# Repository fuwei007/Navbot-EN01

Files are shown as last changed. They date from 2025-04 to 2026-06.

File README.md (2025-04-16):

# NavBot-EN01 Wheeled_leg-Robot
> **The tabletop the tabletop robot**
>
> Vedio:[....](......)

| Real Robot | 3D Design |
| --- | --- |
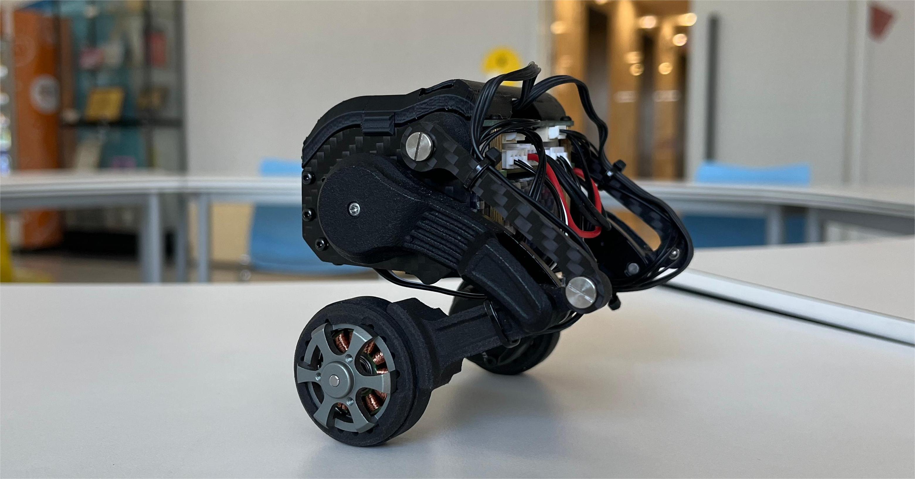
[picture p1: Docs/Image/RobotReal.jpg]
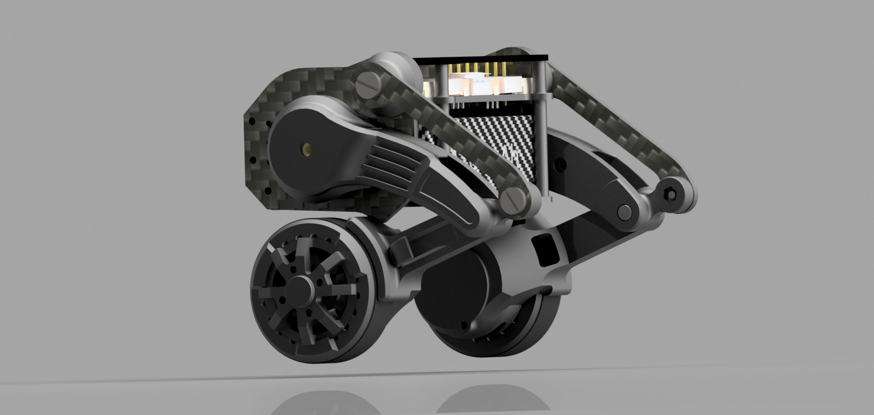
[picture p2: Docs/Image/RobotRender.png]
|  |  |

### Mechanical Structure Documentation

* The file "OriginalRobotModel.stp" is the robot model file.
* The "Parts-Manufactured" folder contains parts that need to be processed and produced by yourself, including 3D printing, CNC, and panel cutting.
* The "Parts-Purchased" folder contains parts that need to be purchased.

### PCB Documentation

* There are four PCBs that need to be fabricated; the circuit boards provide both the schematic and PCB source files, and the IDE used is [LCEDA](https://lceda.cn/).
* The main control board is based on the ESP32, with the brushless motor driver chip being the L6234PD013TR. 
* The encoder chip used is the AS5600, communicating with the main control board via the I2C interface.
* The IMU used is the MPU6050 module, which shares the same I2C interface with the right-side encoder.
* The servo debugging board unifies the two serial lines into one signal line, completing the task through time-division multiplexing to send and receive data.
* In addition, you will need three GH1.25 4PIN double-ended cables, with a recommended length of 15cm. These need to be purchased separately.

| Wire Connection | 
| ------------ |
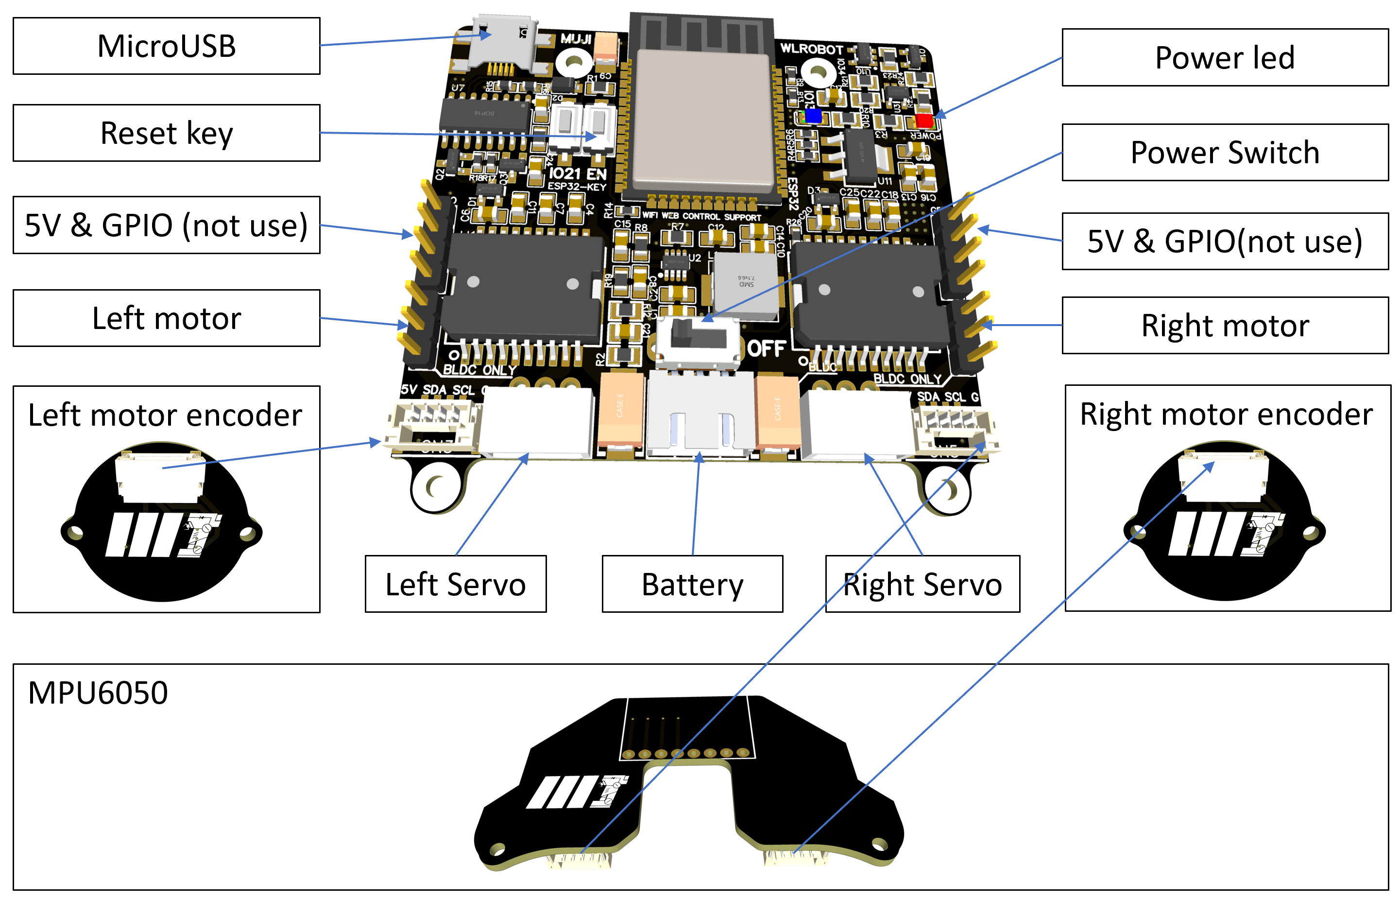
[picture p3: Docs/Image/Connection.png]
|  |

### Source Code Usage

* Based on [Arduino IDE](https://www.arduino.cc/), it is very easy to learn and use.
* The brushless motor drive for the wheels is based on [simpleFOC](https://www.simplefoc.com/#simplefoc_library).
* The left bus servo ID is 1, and the right is 2; the calibration for the legs to fully squat to the mechanical limit position is 2048; configuration is done using [FEETECH Debug Software](https://gitee.com/ftservo/fddebug).
* The [ESP32](https://www.espressif.com/sites/default/files/documentation/esp32_datasheet_en.pdf) itself has WiFi capabilities, with the webpage code stored in flash, transmitting JSON data via the WebSocket communication protocol.
* Please use the WebSocket library located in [3.Software/libraries](3.Software/libraries). The recommended esp32 version is 2.0.3.
* There are two WiFi models, AP mode and STA mode. AP mode uses the device as a wireless hotspot, and STA mode uses the device as a client to connect to an existing wireless network.

### Usage Instructions

* 1. Connect the battery's XH2.54 plug to the rear interface of the main control board and turn on the switch to power the robot.
* 2. After turning on the switch, a red light on the main board will indicate that the power is on.
* 3. Next, the wheels will start FOC motor initialization, with the wheels moving slightly and the legs starting to move.
* 4. If the battery is sufficient, the blue LED on the main control board will light up. If it does not light up, charging is needed.
* 5. After this process is complete, press the EN button on the main control board to restart, and you can then connect to the robot's WiFi network starting with WL. The password is the lowercase WiFi name.
* 6. Open a browser and go to the URL 192.168.1.11. The remote control interface is compatible with Android, iOS, Windows, Linux, macOS, etc., and it is recommended to use Chrome or Firefox.
* 7. Manually stabilize the robot, with the wheels slightly touching the ground. Click the "Robot go!" button on the web page, and the robot will stand up. You can then control the robot's movement using the joystick.

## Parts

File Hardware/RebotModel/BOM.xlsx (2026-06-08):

Part Name | Recommended Purchase Link | Specifications | Quantity | Price($)
Servo | https://www.amazon.com/magnetic-rotating-minibus-steering-black/dp/B0BP645PF9 | 1pcs ST3032 all metal hollow cup 360 degree magnetic coding rotating TTL signal level minibus steering gear (black) | 2 | 110
Motor | https://www.amazon.com/Fityle-Gimbal-Brushless-100-200g-Quadcopter/dp/B07JLSL8ZV | Fityle 2208 90KV 3mm Shaft Gimbal Brushless Motor for 100-200g Gopro3 RC Quadcopter | 2 | 16.31
Neodymium Magnet | https://www.amazon.com/TRYMAG-Magnets-Neodymium-Whiteboard-Billboard/dp/B09SL2K4BP | TRYMAG 340Pcs Small 4x1mm Mini Neodymium Magnets | 2 | 8.99
Battery | https://www.amazon.com/MakerHawk-Rechargeable-Protection-Connector-Electronic/dp/B0D9K7HQHT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 | MakerHawk 4 Pack 3.7V 1000mAh LiPo Battery Rechargeable | 1 | 18.99
Screw M2*4 | https://www.amazon.com/iexcell-Thread-Socket-Screws-Finish/dp/B0D4JM92FW | iexcell 100 Pcs M2 x 4mm | 20 | 7.86
Screw M2*6 | https://www.amazon.com/iexcell-Thread-Socket-Screws-Finish/dp/B0D4JMMJ9M | iexcell 100 Pcs M2 x 6mm | 10 | 7.86
Screw M2.5*5 | https://www.amazon.com/iexcell-Thread-Socket-Screws-Finish/dp/B0DDXRMGCW | iexcell 100 Pcs M2.5 x 5mm | 10 | 7.86
Screw M3*6 | https://www.amazon.com/iexcell-Thread-Socket-Screws-Finish/dp/B07GGXKW1Y | iexcell 250 Pcs M3 x 6 | 4 | 9.86
BigHead Screw M2*6 | https://www.amazon.com/iexcell-Thread-Socket-Screws-Finish/dp/B0D4JMMJ9M | iexcell 100 Pcs M2 x 6mm | 4 | 7.86
Nut M2 | https://www.amazon.com/pouilzx-Carbon-Steel-Hexagon-200pcs/dp/B0CMG7Q27P | M2 Carbon Steel Grade 8 Hexagon Hex Nut Black Carbon Steel | 10 | 5.99
Screw M2.3*15 | https://www.amazon.com/uxcell-Stainless-Phillips-Tapping-Screws/dp/B01M0DCMHQ | uxcell 100 Pcs M2.5 x 15mm Stainless Steel Phillips Round Head Self Tapping Screws Bolts | 2 | 9.29
Earings 3-6-2 | https://www.amazon.com/Hobbypark-Bearings-Shielded-Quadcopter-Helicopter/dp/B019F2ZH92 | 10pcs Hobbypark Micro Ball Bearings 3x6x2mm | 4 | 8.97
Earings 4-7-2.5 | https://www.amazon.com/4x7x2-5-Shielded-Precision-Miniature-Bearings/dp/B085RD75QY | 10 Pack 4x7x2.5 Metal Shielded ABEC-5 High Precision Miniature Ball Bearings L-740ZZ (MR74ZZ) | 4 | 9.49
Cylindrical Pin 4x12 | https://www.amazon.com/uxcell-Stainless-Cylindrical-Support-Elements/dp/B07YKYJZ63 | uxcell 4 x 12mm(Approx 5/32") Dowel Pin 304 Stainless Steel Wood Bunk Bed Dowel Pins Shelf Pegs Support Shelves 25Pcs | 2 | 7.69
Brass Standoff M2*8+3 | https://www.amazon.com/MECCANIXITY-Standoffs-Assortment-Raspberry-Motherboard/dp/B0FH1FTF5J | MECCANIXITY M2 Male Brass Hex Spacer Standoffs Screws Nuts, 20 Set Hex Column Screw Nut Assortment Kit M2*8+3 Threaded Standoff | 2 | 7.69
Brass Standoff M2*25+4 | https://www.amazon.com/PATIKIL-Standoff-Quadcopter-Motherboard-Computer/dp/B0DWF384DG | PATIKIL M2 x 20+3 mm Male Female Brass Hex Spacer Standoff | 2 | 5.09
Brass Standoff M2*8 | https://www.amazon.com/uxcell-Straight-Pillar-Standoff-M2x3x8mm/dp/B07H3SR8XX | uxcell 50pcs Brass Round Straight PCB Pillar Female Thread Standoff Spacer M2x3x8mm | 2 | 7.59
Brass Standoff M2*3*3 | https://www.amazon.com/uxcell-116pcs-Straight-Standoff-M2x3x3mm/dp/B07H3XJ7BB?sp_csd=d2lkZ2V0TmFtZT1zcF9hdGY | uxcell 116pcs Brass Round Straight PCB Pillar Female Thread Standoff Spacer M2x3x3mm | 4 | 8.59
Tire（Round Silicone Ring） | https://www.amazon.com/Rubber-Assorted-Camping-Survival-Supplies/dp/B0BX4CYWB7 | 60 Mixed Count Heavy Duty Rubber Bands 6 Size Black Thick | 2 | 9.99
OLED | https://www.amazon.com/Hosyond-Display-3-3V-5V-Compatible-Raspberry/dp/B0BWJLV39P | 0.91 Inch I2C IIC OLED Display Module OLED | 1 | 13.99
sh1.0 4P | https://www.amazon.com/Pre-Crimped-Connectors-SPRacingF3-Omnibus-Silicone/dp/B07PDQKHJ2 | SH1.0 Connectors and Pre-Crimped Silicone Cables Compatible with JST SH 1.0mm | 2 | 19.99
MX1.27 7P | https://www.amazon.com/HFHYDZSW-MX1-25-1-25mm-Connector-Head_10PCS_7P/dp/B0DSTVJBH2 | HFHYDZSW 10PCS JST 10mm Wire Cable | 1 | 19.26

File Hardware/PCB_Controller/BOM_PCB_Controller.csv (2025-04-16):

ID | Name | Designator | Footprint | Quantity | Manufacturer Part | Manufacturer
1 | 4.7K | R26,R4,R5,R6,R9,R13,R14 | R0603 | 7
2 | 0.1uF | C23,C24,C2,C8,C12 | C0805 | 5 |  | LCSC
3 | 1N4007W | D2 | SOD-123_L2.8-W1.8-LS3.7-RD | 1 | 1N4007W | BLUE ROCKET
4 | CH340C | U7 | SOP-16_L10.0-W3.9-P1.27-LS6.0-BL | 1 | CH340C | WCH(南京沁恒)
5 | 0.1uF | C21,C17,C19 | C0805 | 3 | CC0805KRX7R9BB104 | YAGEO
6 | SS-12D02-VG4 | CN7 | SW-TH_SS-12D02-VG4 | 1 | SS-12D02-VG4 | Rectangular Connectors - Contacts
7 | 3K/0.1% | R2 | R0805 | 1 | TC0525B3001T5E | UniOhm
8 | 1k/0.1% | R12 | R0805 | 1 | ARG05BTC1001 | Viking Tech
9 | 5264-3A | H10,H11 | CONN-TH_5264-3AW | 2
10 | SS8050_C541705 | Q2,Q3 | SOT-23-3_L2.9-W1.3-P1.90-LS2.4-BR | 2 | SS8050 | AnBon
11 | 1K | R15,R16 | R0603 | 2 | RMCF0603JT10K0 | Stackpole Elec
12 | 10K | R17,R18 | R0603 | 2 | RMCF0603JT10K0 | Stackpole Elec
13 | HDR-M-2.54_1x4 | J2,J4 | HDR-M-2.54_1X4 | 2
14 | U-C-M5SS-Y-1 | USB2 | MICRO-USB-SMD_U-C-M5SS-Y-1 | 1 | U-C-M5SS-Y-1 | 韩国韩荣
15 | HX25003-3WAP | CN2 | CONN-TH_3P-P2.50_HX25003-3WAP | 1 | HX25003-3WAP | HX(红星)
16 | LED-0805_B | LED2 | LED0805_BLUE | 1 | D-B080508B1-KS2 | 方舟 ARKLED
17 | 1K | R10,R3 | R0805 | 2 | 0805W8F1001T5E | UniOhm
18 | LED-0805_R | LED1 | LED0805_RED | 1 | 17-21SURC/S530-A3/TR8 | EVERLIGHT(台湾亿光)
19 | 10uF | C16,C13 | C0805 | 2 | CL21A106KOQNNNE | SAMSUNG
20 | 22uF | C1,C10,C14 | C0805 | 3
21 | 33pF | C15 | C0805 | 1
22 | 4.7uH | L1 | IND-SMD_L7.3-W6.6 | 1 | MCS0630-4R7MPY1 | PSA(信昌电陶)
23 | SS8550-C148468 | Q1 | SOT-23-3_L2.9-W1.3-P1.90-LS2.4-BR | 1 | SS8550 | Yenji
24 | 100k | R7 | R0805 | 1
25 | 40.2k | R8 | R0805 | 1
26 | 5.49k | R19 | R0805 | 1
27 | 10k | R20,R21,R23,R24 | R0805 | 4 | 0805W8F1002T5E | UniOhm
28 | 10k | R22 | R0805 | 1 | 0805W8F2002T5E | UniOhm
29 | MP2225GJ-Z | U2 | TSOT-23-8_L2.9-W1.6-P0.65-LS2.8-BR | 1 | MP2225GJ-Z | MPS
30 | SN74LVC1G125DBVR | U3 | SOT-23-5_L3.0-W1.7-P0.95-LS2.8-BR | 1 | SN74LVC1G125DBVR | TI
31 | SN74LVC1G126DBVR | U10 | SOT-23-5_L3.0-W1.7-P0.95-LS2.8-BR | 1 | SN74LVC1G126DBVR | TI
32 | 100uF | C9 | CAP-SMD_L3.5-W2.8-R-RD | 1 | CA45-B-6.3V-100uF-M | Shenzhen Zhenhua XinYun Elec
33 | AMS1117-3.3 | U11 | SOT-223_L6.7-W3.5-P2.30-BR | 1 | AMS1117-3.3 | Youtai Semiconductor Co., Ltd.
34 | 100uF | C3,C5 | CAP-SMD_L7.3-W4.3-R-RD | 2 | TAJD107M020RNJ | AVX
35 | A1257WV-S-4P | CN3,CN5 | CONN-SMD_A1257WV-S-4P | 2 | A1257WV-S-4P | Changjiang Connectors
36 | HDR-M-2.54_1x3 | J1,J3 | HDR-M-2.54_1X3 | 2
37 | 10K | R1,R11 | R0805 | 2 | RMCF0603JT10K0 | Stackpole Elec
38 | 100nF | C4,C18 | C0805 | 2 | C0805X104K101T | HEC(Holy Stone Enterprise)
39 | 220nF | C6,C20 | C0805 | 2 | CL21B224KBFNNNE | SAMSUNG
40 | 1uF | C7,C22 | C0805 | 2 | CL21B105KBFNNNE | SAMSUNG
41 | 10nF | C11,C25 | C0805 | 2 | CL21A106KAYNNNE | SAMSUNG
42 | LBAT54SLT1G | D1,D3 | SOT-23_L2.9-W1.3-P1.90-LS2.4-BR | 2 | LBAT54SLT1G | LRC
43 | K2-3.6×6.1_SMD | KEY1,KEY2 | KEY-SMD_2P-L6.2-W3.6-LS8.0 | 2 | K2-1107ST-A4SW-06
44 | L6234PD013TR | U1,U4 | POWERSO20_L15.9-W11.0-P1.27-LS14.2-BL-EP | 2 | L6234PD013TR | STMicroelectronics
45 | ESP32-WROOM-32 | U5 | WIFIM-SMD_ESP-32S | 1 | ESP32-WROOM-32 | Espressif Systems

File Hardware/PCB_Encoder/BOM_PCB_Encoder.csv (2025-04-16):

ID | Name | Designator | Footprint | Quantity | Manufacturer Part | Manufacturer
1 | GH1.25_4P | J2 | GH1.25_4P_卧贴 | 1 |  | Changjiang Connectors
2 | 100nf | C1 | C0603 | 1
3 | 1uf | C2 | C0603 | 1
4 | 4.7K | R1,R2 | R0603 | 2
5 | AS5600-ASOM | U1 | SOIC-8_L5.0-W4.0-P1.27-LS6.0-BL | 1 | AS5600-ASOM | Ams

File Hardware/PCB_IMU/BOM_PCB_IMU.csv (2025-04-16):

ID | Name | Designator | Footprint | Quantity | Manufacturer Part | Manufacturer
1 | MPU6050模块 | P2 | MPU6050 | 1
2 | GH1.25_4P | J2,J1 | GH1.25_4P_卧贴 | 2 |  | Changjiang Connectors

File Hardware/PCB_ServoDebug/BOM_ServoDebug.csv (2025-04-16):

ID | Name | Designator | Footprint | Quantity | Manufacturer Part | Manufacturer
1 | HDR-F-2.54_2x4 | H1 | HDR-F-2.54_2X4 | 1
2 | 0.1uF | C1,C2 | C0805 | 2 | CC0805KRX7R9BB104 | YAGEO
3 | WJ126V-5.0-2P | P3 | CONN-TH_WJ126V-5.0-2P | 1 | WJ126V-5.0-2P | ReliaPro
4 | SS8550 | Q1 | SOT-23_L2.9-W1.3-P0.95-LS2.4-BR | 1 | SS8550 | Slkor(SLKORMICRO Elec.)
5 | 10k | R1,R2,R3,R4,R5 | R0805 | 4 | 0805W8F1002T5E | UniOhm
6 | SN74LVC1G126DBVR | U2 | SOT-23-5_L3.0-W1.7-P0.95-LS2.8-BR | 1 | SN74LVC1G125DBVR | TI
7 | SN74LVC1G125DBVR | U3 | SOT-23-5_L3.0-W1.7-P0.95-LS2.8-BR | 1 | SN74LVC1G125DBVR | TI
8 | 5264-3A | H2 | 5264-3A | 1

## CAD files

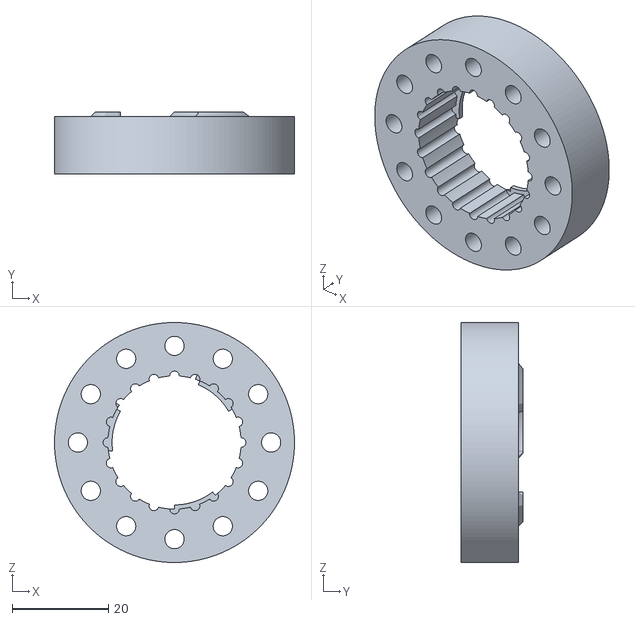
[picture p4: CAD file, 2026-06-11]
Hardware/RebotModel/3D_print/#Large_Wheel.stl
50.0 x 13.0 x 50.0

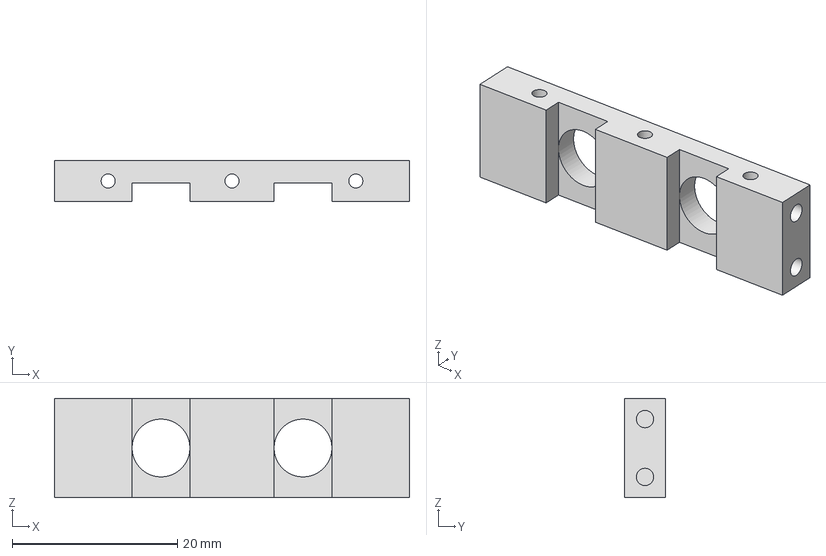
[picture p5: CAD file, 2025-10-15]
Hardware/RebotModel/CNC/MotorBase-Aluminum6061.stp
43.0 x 5.00 x 12.0 mm

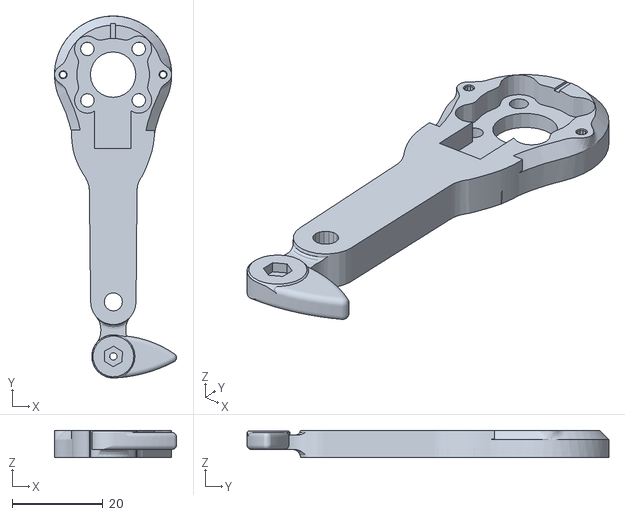
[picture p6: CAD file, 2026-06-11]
Hardware/RebotModel/3D_print/#Large_Wheel_CalfR.stl
26.9 x 79.6 x 6.02

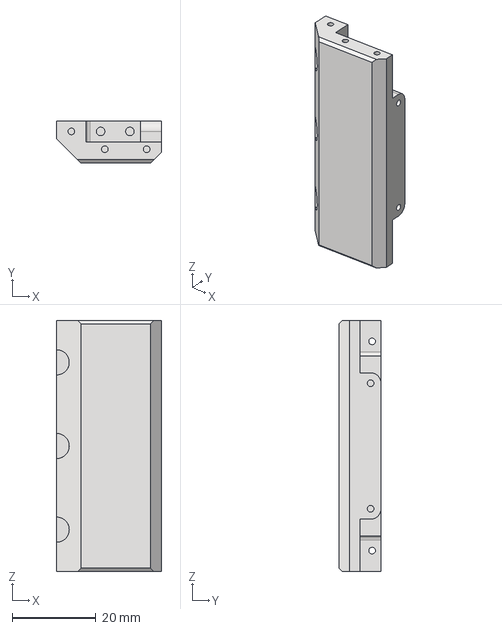
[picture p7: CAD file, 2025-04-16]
Hardware/RebotModel/CNC/BodyBase-Steel.stp
25.0 x 10.1 x 60.0 mm

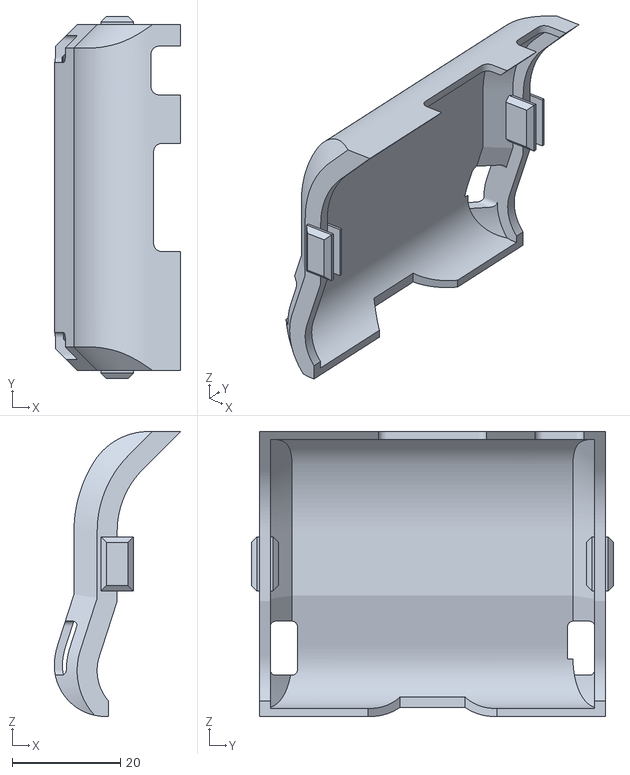
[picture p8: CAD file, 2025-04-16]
Hardware/RebotModel/3D_print/PCB_Cover(optional).stl
23.4 x 67.0 x 52.7

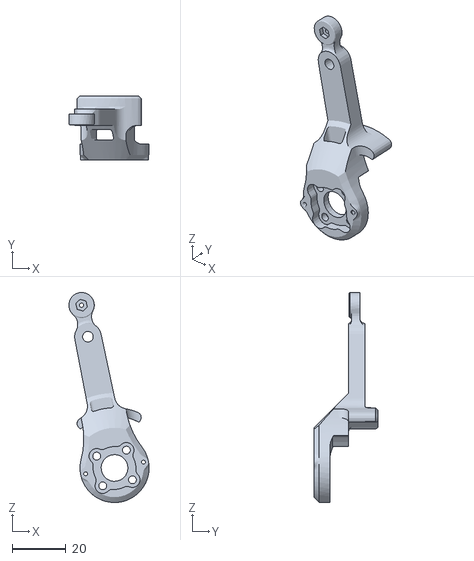
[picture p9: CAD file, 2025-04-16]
Hardware/RebotModel/3D_print/Calf x1.stl
29.9 x 24.0 x 78.4

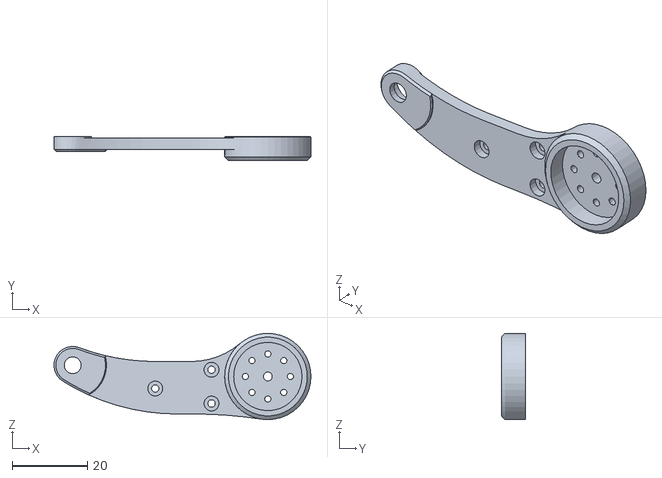
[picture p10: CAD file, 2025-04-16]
Hardware/RebotModel/3D_print/Thigh_MIR x1.stl
68.5 x 6.50 x 23.0

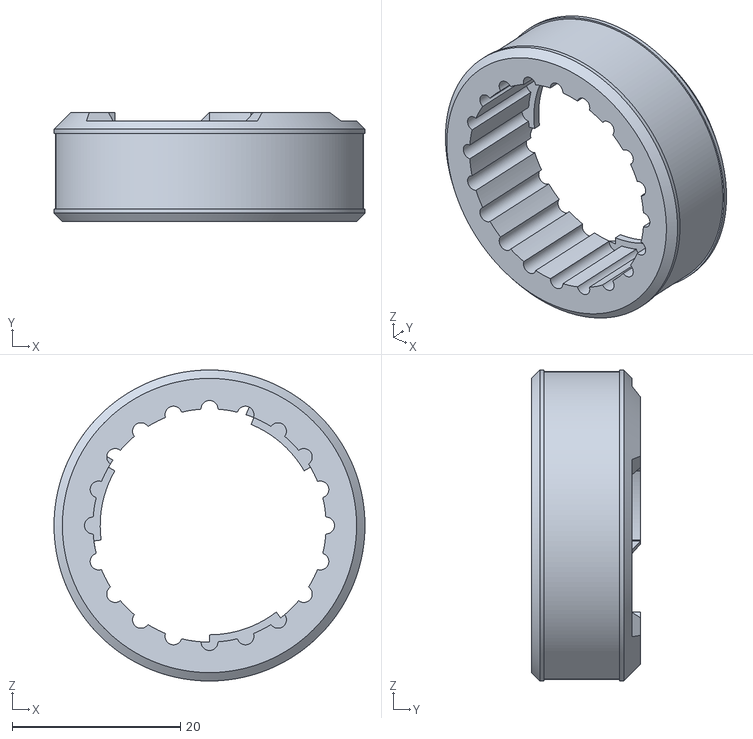
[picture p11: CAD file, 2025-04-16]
Hardware/RebotModel/3D_print/Hub x2.stl
37.0 x 13.0 x 37.0

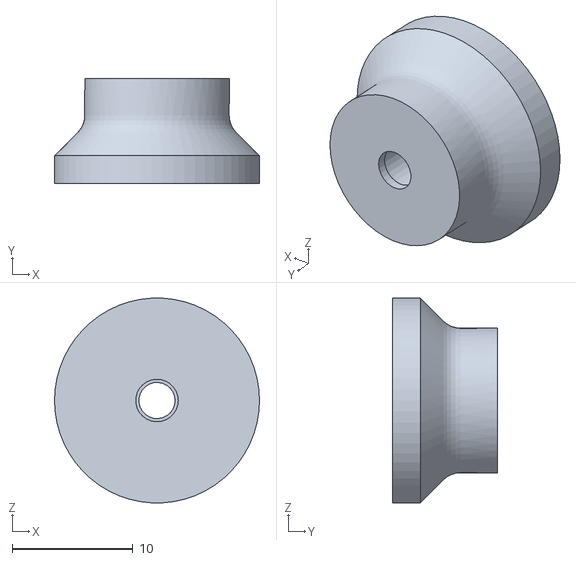
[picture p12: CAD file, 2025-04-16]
Hardware/RebotModel/3D_print/ColumnCover x2.stl
17.0 x 8.70 x 17.0

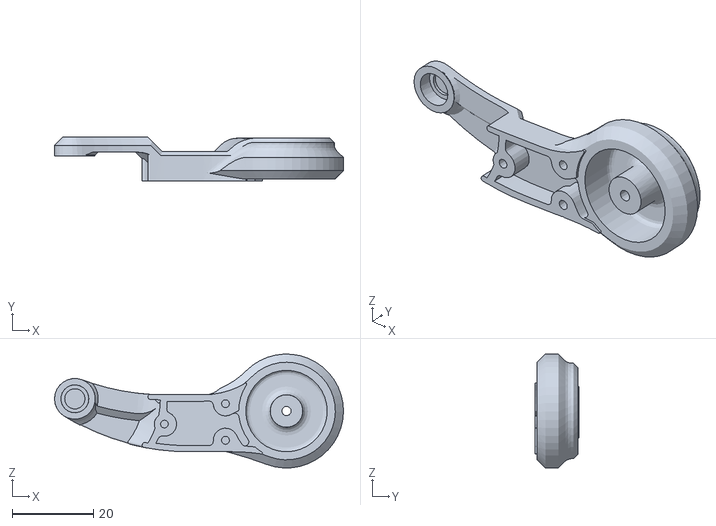
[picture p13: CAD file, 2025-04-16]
Hardware/RebotModel/3D_print/Thigh_Cover_R x1.stl
71.0 x 10.8 x 28.0

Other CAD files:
Hardware/RebotModel/CarbonFiberPanels/Panel.dwg
Hardware/RebotModel/3D_print/#Large_Wheel_CalfL.stl
Hardware/RebotModel/3D_print/Calf_MIR x1.stl
Hardware/RebotModel/3D_print/Thigh_Cover_L x1.stl
Hardware/RebotModel/3D_print/Thigh x1.stl

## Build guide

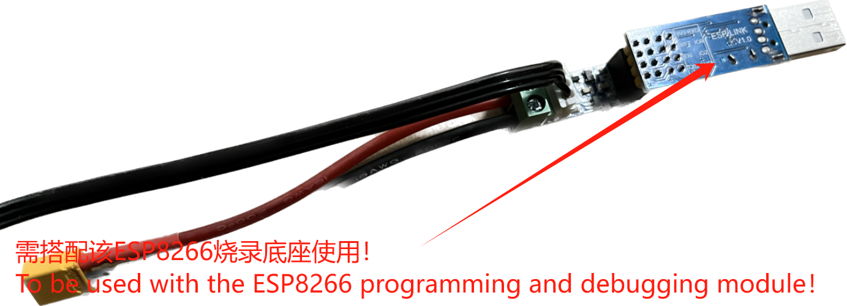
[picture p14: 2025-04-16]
Hardware/PCB_ServoDebug/SpecialInstruction.png

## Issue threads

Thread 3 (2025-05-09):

Please Add Credit to the Original Author

MuShibo, 2025-05-09:
Hi, I noticed your video uses my GitHub project (https://github.com/MuShibo/Micro-Wheeled_leg-Robot). Please add proper credit and a link to the original project in the description. Thank you.

fuwei007, 2025-05-09:
Thanks @MuShibo

Thank you for reaching out and for your great work on the Micro-Wheeled Leg Robot project. I truly appreciate your contribution and apologize for the oversight. I've now updated the readme file include proper credit and a link to your original GitHub project. As well as the description in the video description.

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

Please let me know if there's anything else you'd like me to add to follow the license of the project.

Thanks again!

Frank

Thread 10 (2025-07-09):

Add health info and device info

nullhat2, 2025-07-09:
{
  BatteryPercentage : 80
  BatteryVotage:15.1
  Temperature: 21.3
  Status:0/1/2
}
{
  ESP32: 2.0.1
  Main: 1.0.1
  GPS:....
}

Closed 2025-08-04.

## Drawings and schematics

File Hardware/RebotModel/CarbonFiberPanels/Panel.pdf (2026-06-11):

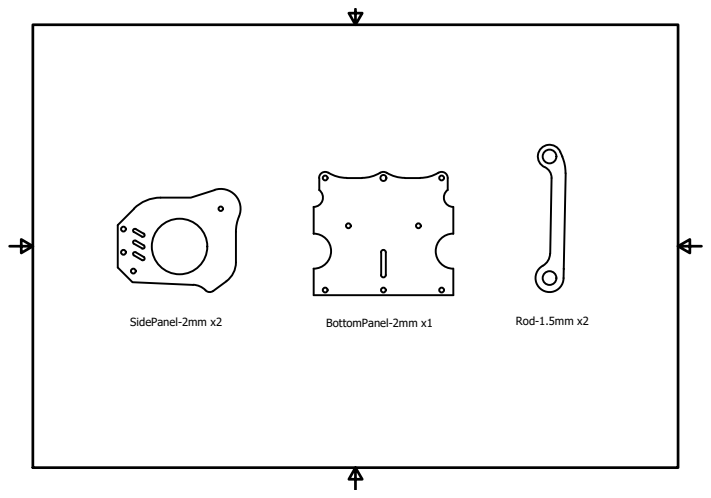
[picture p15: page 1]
SidePanel-2mm x2; BottomPanel-2mm x1; Rod-1.5mm x2

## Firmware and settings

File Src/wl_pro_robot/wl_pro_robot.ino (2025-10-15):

//Robot controlled header file
#include <MPU6050_tockn.h>
#include "Servo_STS3032.h"
#include <SimpleFOC.h>
#include <Arduino.h>

//WiFi transmission header file
#include <WebSocketsServer.h>
#include <ArduinoJson.h>
#include <WebServer.h>
#include <WiFi.h>
#include <FS.h>
#include "basic_web.h"
#include "robot.h"
#include "wifi.h"
#include "esp_adc_cal.h"
#include "ble.h"
#include "EEPROM.h"
#include "eeprom_util.h"
#include "feedback_util.h"
#include "web_socket_client_util.h"
 
#include "cpu0_task.h"

/************Instance definition*************/

//Electromotor instance
BLDCMotor motor1 = BLDCMotor(7);
BLDCMotor motor2 = BLDCMotor(7);
BLDCDriver3PWM driver1 = BLDCDriver3PWM(32, 33, 25, 22);
BLDCDriver3PWM driver2 = BLDCDriver3PWM(26, 27, 14, 12);

//Encoder instance
TwoWire I2Cone = TwoWire(0);
TwoWire I2Ctwo = TwoWire(1);
MagneticSensorI2C sensor1 = MagneticSensorI2C(AS5600_I2C);
MagneticSensorI2C sensor2 = MagneticSensorI2C(AS5600_I2C);

//PID instance
PIDController pid_angle{ .P = 1, .I = 0, .D = 0, .ramp = 100000, .limit = 8 };
PIDController pid_gyro{ .P = 0.06, .I = 0, .D = 0, .ramp = 100000, .limit = 8 };
PIDController pid_distance{ .P = 0.5, .I = 0, .D = 0, .ramp = 100000, .limit = 8 };
PIDController pid_speed{ .P = 0.7, .I = 0, .D = 0, .ramp = 100000, .limit = 8 };
PIDController pid_yaw_angle{ .P = 1.0, .I = 0, .D = 0, .ramp = 100000, .limit = 8 };
PIDController pid_yaw_gyro{ .P = 0.04, .I = 0, .D = 0, .ramp = 100000, .limit = 8 };
PIDController pid_lqr_u{ .P = 1, .I = 15, .D = 0, .ramp = 100000, .limit = 8 };
PIDController pid_zeropoint{ .P = 0.002, .I = 0, .D = 0, .ramp = 100000, .limit = 4 };
PIDController pid_roll_angle{ .P = 8, .I = 0, .D = 0, .ramp = 100000, .limit = 450 };

//Low pass filter instance
LowPassFilter lpf_joyy{ .Tf = 0.2 };
LowPassFilter lpf_zeropoint{ .Tf = 0.1 };
LowPassFilter lpf_roll{ .Tf = 0.3 };

// Commander instance
Commander command = Commander(Serial);

void StabAngle(char* cmd) {
  command.pid(&pid_angle, cmd);
}
void StabGyro(char* cmd) {
  command.pid(&pid_gyro, cmd);
}
void StabDistance(char* cmd) {
  command.pid(&pid_distance, cmd);
}
void StabSpeed(char* cmd) {
  command.pid(&pid_speed, cmd);
}
void StabYawAngle(char* cmd) {
  command.pid(&pid_yaw_angle, cmd);
}
void StabYawGyro(char* cmd) {
  command.pid(&pid_yaw_gyro, cmd);
}
void lpfJoyy(char* cmd) {
  command.lpf(&lpf_joyy, cmd);
}
void StabLqrU(char* cmd) {
  command.pid(&pid_lqr_u, cmd);
}
void StabZeropoint(char* cmd) {
  command.pid(&pid_zeropoint, cmd);
}
void lpfZeropoint(char* cmd) {
  command.lpf(&lpf_zeropoint, cmd);
}
void StabRollAngle(char* cmd) {
  command.pid(&pid_roll_angle, cmd);
}
void lpfRoll(char* cmd) {
  command.lpf(&lpf_roll, cmd);
}

bool one_second_tick(void);
bool ten_msec_tick(void);
//void Stabtest_zeropoint(char* cmd) { command.pid(&test_zeropoint, cmd); }

//WebServer instance
WebServer webserver;                                // server
WebSocketsServer websocket = WebSocketsServer(81);  // Define a webSocket server to process messages sent by clients
int joystick_value[2];

//MPU6050 instance
MPU6050 mpu6050(I2Ctwo);

/************parameter definition*************/
#define pi 3.1415927

//LQR Self-balancing controller parameters
float LQR_angle = 0;
float LQR_gyro = 0;
float LQR_speed = 0;
float LQR_distance = 0;
float angle_control = 0;
float gyro_control = 0;
float speed_control = 0;
float distance_control = 0;
float LQR_u = 0;
float angle_zeropoint = 4.02;
float distance_zeropoint = -256.0;  //Wheel position shift zero offset \
 (-256 is an impossible displacement value, use it as a sign that it is not refreshed)


//YAW axis control data
float YAW_gyro = 0;
float YAW_angle = 0;
float YAW_angle_last = 0;
float YAW_angle_total = 0;
float YAW_angle_zero_point = -10;
float YAW_output = 0;

//Leg steering gear control data
byte ID[2];
s16 Position[2];
u16 Speed[2];
byte ACC[2];

//Logical processing flag bit
float robot_speed = 0;          //Record the current wheel speed
float robot_speed_last = 0;     //Record the wheel speed at the previous time
int wrobot_move_stop_flag = 0;  //Record the sign that the rocker stops
int jump_flag = 0;              //Jump period identification
float leg_position_add = 0;     //roll axis balance control quantity

//Voltage detection

static const adc1_channel_t channel = ADC1_CHANNEL_7;
// static const adc_bits_width_t width = ADC_WIDTH_BIT_12;
static const adc_atten_t atten = ADC_ATTEN_DB_11;
static const adc_unit_t unit = ADC_UNIT_1;

//Power display LED Pin
#define LED_BAT 13

void user_function(char* cmd) {
  if (*cmd == '{') {
    rp.json_test(cmd);
  }
}

void setup() {
  Serial.begin(2000000);
  Serial2.begin(1000000);
  rp.get_pcb_version();
  rp.config_json_init();
  ble_init();
  wifi_init();
  if (get_wifi_state() != WIFI_STATE.CLOSE) {
    webserver.begin();
    webserver.on("/", HTTP_GET, basicWebCallback);
    websocket.begin();
    websocket.onEvent(webSocketEventCallback);
  }

  web_sockets_client_init();

  xTaskCreatePinnedToCore(cpu0_task, "cpu0_task", 2048, NULL, 0, NULL, 0);

  //Steering gear initialization
  //Steering gear effective stroke 450
  //Left-hand steering gear[2048+12+50,2048+12+450]
  //Right-hand steering gear[2048-12-50,2048-12-450]
  sms_sts.pSerial = &Serial2;
  ID[0] = 1;
  ID[1] = 2;
  ACC[0] = 30;
  ACC[1] = 30;
  Speed[0] = 300;
  Speed[1] = 300;
  Position[0] = 2048;
  Position[1] = 2048;
  //The steering gear (ID1/ID2) runs to their respective positions at maximum speed V=2400 steps/SEC and \
  acceleration A=50(50*100 steps/SEC ^2)
  sms_sts.SyncWritePosEx(ID, 2, Position, Speed, ACC);

  //Voltage detection
  adc_calibration_init();
  adc1_config_width(ADC_WIDTH_BIT_12);
  adc1_config_channel_atten(channel, atten);
  esp_adc_cal_characterize(unit, atten, ADC_WIDTH_BIT_12, 0, &adc_chars);

  //Voltage detection LED
  pinMode(LED_BAT, OUTPUT);

  // Encoder setup
  I2Cone.begin(19, 18, 400000UL);
  I2Ctwo.begin(23, 5, 400000UL);
  sensor1.init(&I2Cone);
  sensor2.init(&I2Ctwo);

  //mpu6050 setup
  mpu6050.begin();
  mpu6050.calcGyroOffsets(true);

  //Connect the motor object to the encoder object
  motor1.linkSensor(&sensor1);
  motor2.linkSensor(&sensor2);

  //Speed loop PID parameter
  motor1.PID_velocity.P = 0.05;
  motor1.PID_velocity.I = 1;
  motor1.PID_velocity.D = 0;

  motor2.PID_velocity.P = 0.05;
  motor2.PID_velocity.I = 1;
  motor2.PID_velocity.D = 0;

  // Motor driver setup
  motor1.voltage_sensor_align = 6;
  motor2.voltage_sensor_align = 6;
  driver1.voltage_power_supply = 8;
  driver2.voltage_power_supply = 8;
  driver1.init();
  driver2.init();

  //Connect the motor object to the drive object
  motor1.linkDriver(&driver1);
  motor2.linkDriver(&driver2);

  motor1.torque_controller = TorqueControlType::voltage;
  motor2.torque_controller = TorqueControlType::voltage;
  motor1.controller = MotionControlType::torque;
  motor2.controller = MotionControlType::torque;

  // Motor-related Settings
  motor1.useMonitoring(Serial);
  motor2.useMonitoring(Serial);
  //init
  motor1.init();
  motor1.initFOC();
  motor2.init();
  motor2.initFOC();

  // Map motor to commander
  command.add('A', StabAngle, "pid angle");
  command.add('B', StabGyro, "pid gyro");
  command.add('C', StabDistance, "pid distance");
  command.add('D', StabSpeed, "pid speed");
  command.add('E', StabYawAngle, "pid yaw angle");
  command.add('F', StabYawGyro, "pid yaw gyro");
  command.add('G', lpfJoyy, "lpf joyy");
  command.add('H', StabLqrU, "pid lqr u");
  command.add('I', StabZeropoint, "pid zeropoint");
  command.add('J', lpfZeropoint, "lpf zeropoint");
  command.add('K', StabRollAngle, "pid roll angle");
  command.add('L', lpfRoll, "lpf roll");
  command.add('U', user_function, "user function");

  //command.add('M', Stabtest_zeropoint, "test_zeropoint");
  delay(500);
}

void loop() {

  if (one_second_tick()) {
    bat_check();  //Voltage detection
    wifi_loop();
    static int ttss;
    Serial.println(ttss++);
  }
  if (ten_msec_tick()) {
    ble_loop();
    rp.test_log_output();
    // show_expression_time_callback(10);
  }

  web_loop();  //Web data update

  mpu6050.update();    //IMU data update
  lqr_balance_loop();  //lqr self-balancing control
  yaw_loop();          //yaw axis steering control
  leg_loop();          //Leg motion control

  //The self-balancing calculated output torque is assigned to the motor
  motor1.target = (-0.5) * (LQR_u + YAW_output);
  motor2.target = (-0.5) * (LQR_u - YAW_output);
 


  //Shut down output after falling out of control
  
  if (abs(LQR_angle) > rp.uncontrolable_angle) {
    rp.uncontrolable = 1;
  }
  if (rp.uncontrolable != 0)  //Delay recovery after lifting
  {
    if (abs(LQR_angle) < 15.0f) {
      rp.uncontrolable++;
    }
    if (rp.uncontrolable > 200)  //The delay time of 200 program cycles
    {
     rp.uncontrolable = 0;
    }
  }

  //Turn off output (remote control stop or Angle is too large out of control)
  if (wrobot.go == 0 || rp.uncontrolable != 0) {
    motor1.target = 0;
    motor2.target = 0;
    leg_position_add = 0;
    wrobot.joyx = 0;
    wrobot.joyy = 0;
    wrobot.roll = 0;
    wrobot.height = 34;
  }

  //Record the last remote control data
  wrobot.dir_last = wrobot.dir;
  wrobot.joyx_last = wrobot.joyx;
  wrobot.joyy_last = wrobot.joyy;

  //The FOC phase voltage is computed iteratively
  motor1.loopFOC();
  motor2.loopFOC();

  //Set the wheel motor output
  motor1.move();
  motor2.move();

  command.run();
}

//lqr self-balancing control
void lqr_balance_loop() {
  /*
  * LQR balance formula, in order to facilitate the adjustment of parameters in actual use, 
  * the formula is decomposed into 4 P controls, 
  * using the PIDController method in commander real-time debugging
  */
  //QR_u = LQR_k1*(LQR_angle - angle_zeropoint) + LQR_k2*LQR_gyro + LQR_k3*(LQR_distance - distance_zeropoint) + LQR_k4*LQR_speed;

  //The negative value is given because, according to the current motor wiring, the positive torque will turn backwards
  LQR_distance = (-0.5) * (motor1.shaft_angle + motor2.shaft_angle);
  LQR_speed = (-0.5) * (motor1.shaft_velocity + motor2.shaft_velocity);
  LQR_angle = (float)mpu6050.getAngleY();
  LQR_gyro = (float)mpu6050.getGyroY();
  //Serial.println(LQR_distance);
  // Serial.println(LQR_angle);
  // Serial.print("-->");
  // Serial.println(angle_control);
  //Calculate self-balancing output
  angle_control = pid_angle(LQR_angle - angle_zeropoint);
  gyro_control = pid_gyro(LQR_gyro);

  //Motion detail optimization processing
  if (wrobot.joyy != 0)  //Handling when there are forward and backward direction motion instructions
  {
    distance_zeropoint = LQR_distance;  //Displacement zero reset
    pid_lqr_u.error_prev = 0;           //The output integral is cleared to zero
  }

  if ((wrobot.joyx_last != 0 && wrobot.joyx == 0) || (wrobot.joyy_last != 0 && wrobot.joyy == 0))  //Stop in place processing when motion instruction returns to zero
  {
    wrobot_move_stop_flag = 1;
  }
  if ((wrobot_move_stop_flag == 1) && (abs(LQR_speed) < 0.5)) {
    distance_zeropoint = LQR_distance;  //Displacement zero reset
    wrobot_move_stop_flag = 0;
  }

  if (abs(LQR_speed) > 15)  //Stop in place treatment when being pushed rapidly
  {
    distance_zeropoint = LQR_distance;  //Displacement zero reset
  }

  //Calculate displacement control output
  distance_control = pid_distance(LQR_distance - distance_zeropoint);
  speed_control = pid_speed(LQR_speed - 0.1 * lpf_joyy(wrobot.joyy));

  //Wheel lift detection
  robot_speed_last = robot_speed;  //Record two consecutive wheel speeds
  robot_speed = LQR_speed;
  if (abs(robot_speed - robot_speed_last) > 10 || abs(robot_speed) > 50 || (jump_flag != 0)) /*If the angular speed and angular acceleration of the 
                                                    wheel are too large or in the recovery period after jumping, 
                                                    it is considered that the wheel is off the 
                                                    ground and needs special treatment.
                                                  */
  {
    distance_zeropoint = LQR_distance;     //Displacement zero point reset
    LQR_u = angle_control + gyro_control;  //When the wheel part is off the ground, \
                                          the quantity of the opposite wheel part is not output.\
                                          Conversely, under normal conditions, the balanced torque is fully output
    pid_lqr_u.error_prev = 0;              //The output integral is reset to zero
  } else {
    LQR_u = angle_control + gyro_control + distance_control + speed_control;
  }

  //Trigger conditions: No signal input from the remote control, \
    normal intervention of the wheel position movement control, \
    and not in the recovery period after jumping
  if (abs(LQR_u) < 5 && wrobot.joyy == 0 && abs(distance_control) < 4 && (jump_flag == 0)) {

    LQR_u = pid_lqr_u(LQR_u);  //Compensate for the nonlinearity of small torque
    //Serial.println(LQR_u);
    angle_zeropoint -= pid_zeropoint(lpf_zeropoint(distance_control));  //Center of gravity adaptive
  } else {
    pid_lqr_u.error_prev = 0;  //The output integral is reset to zero
  }

  //The balance control parameters are adaptive
  if (wrobot.height < 50) {
    pid_speed.P = 0.7;
  } else if (wrobot.height < 64) {
    pid_speed.P = 0.6;
  } else {
    pid_speed.P = 0.5;
  }
}

//Leg movement control
void leg_loop() {
  jump_loop();
  if (jump_flag == 0)  //Not in a jumping state
  {
    static s16 last_Position[2];
    //Adaptive control of the body height
    ACC[0] = 5;
    ACC[1] = 5;
    Speed[0] = 150;
    Speed[1] = 150;
    float roll_angle = (float)mpu6050.getAngleX() + rp.offset_roll;
    // leg_position_add += pid_roll_angle(roll_angle);
    leg_position_add = pid_roll_angle(lpf_roll(roll_angle));  //test
    Position[0] = 2048 + 8.4 * (wrobot.height - 32) - leg_position_add;
    Position[1] = 2048 - 8.4 * (wrobot.height - 32) - leg_position_add;
    if (Position[0] < 2110)
      Position[0] = 2110;
    else if (Position[0] > 2510)
      Position[0] = 2510;
    if (Position[1] < 1586)
      Position[1] = 1586;
    else if (Position[1] > 1986)
      Position[1] = 1986;

    if((last_Position[1] != Position[1])  || (last_Position[0] != Position[0]))
    {
      last_Position[0] = Position[0];
      last_Position[1] = Position[1];
      sms_sts.SyncWritePosEx(ID, 2, Position, Speed, ACC);
    }
    
  }
}

//Jump control
void jump_loop() {
  if ((wrobot.dir_last == STOP) && (wrobot.dir == JUMP) && (jump_flag == 0)) {
    ACC[0] = 0;
    ACC[1] = 0;
    Speed[0] = 0;
    Speed[1] = 0;
    Position[0] = 2048 + 12 + 8.4 * (80 - 32);
    Position[1] = 2048 - 12 - 8.4 * (80 - 32);
    sms_sts.SyncWritePosEx(ID, 2, Position, Speed, ACC);

    jump_flag = 1;
  }
  if (jump_flag > 0) {
    jump_flag++;
    if ((jump_flag > 30) && (jump_flag < 35)) {
      ACC[0] = 0;
      ACC[1] = 0;
      Speed[0] = 0;
      Speed[1] = 0;
      Position[0] = 2048 + 12 + 8.4 * (40 - 32);
      Position[1] = 2048 - 12 - 8.4 * (40 - 32);
      sms_sts.SyncWritePosEx(ID, 2, Position, Speed, ACC);

      jump_flag = 40;
    }
    if (jump_flag > 200) {
      jump_flag = 0;  //Ready to jump again
    }
  }
}

//yaw axis steering control
void yaw_loop() {
  //YAW_output = 0.03*(YAW_Kp*YAW_angle_total + YAW_Kd*YAW_gyro);
  yaw_angle_addup();

  YAW_angle_total += wrobot.joyx * 0.002;
  float yaw_angle_control = pid_yaw_angle(YAW_angle_total);
  float yaw_gyro_control = pid_yaw_gyro(YAW_gyro);
  YAW_output = yaw_angle_control + yaw_gyro_control;

}

//Web Data Update
void web_loop() {
  webserver.handleClient();
  websocket.loop();
  web_sockets_client_loop();  // The websocket client continuously makes requests.
  rp.spinOnce();              //Update the control information returned by the web end
}

//The yaw axis Angle accumulation function
void yaw_angle_addup() {
  YAW_angle = (float)mpu6050.getAngleZ();
  YAW_gyro = (float)mpu6050.getGyroZ();

  if (YAW_angle_zero_point == (-10)) {
    YAW_angle_zero_point = YAW_angle;
  }

  float yaw_angle_1, yaw_angle_2, yaw_addup_angle;
  if (YAW_angle > YAW_angle_last) {
    yaw_angle_1 = YAW_angle - YAW_angle_last;
    yaw_angle_2 = YAW_angle - YAW_angle_last - 2 * PI;
  } else {
    yaw_angle_1 = YAW_angle - YAW_angle_last;
    yaw_angle_2 = YAW_angle - YAW_angle_last + 2 * PI;
  }

  if (abs(yaw_angle_1) > abs(yaw_angle_2)) {
    yaw_addup_angle = yaw_angle_2;
  } else {
    yaw_addup_angle = yaw_angle_1;
  }

  YAW_angle_total = YAW_angle_total + yaw_addup_angle;
  YAW_angle_last = YAW_angle;
}

void basicWebCallback(void) {
  webserver.send(300, "text/html", basic_web);
}

void webSocketEventCallback(uint8_t num, WStype_t type, uint8_t* payload, size_t length) {
  if (type == WStype_TEXT) {
    String payload_str = String((char*)payload);
    StaticJsonDocument<300> doc;
    DeserializationError error = deserializeJson(doc, payload_str);

    String mode_str = doc["mode"];
    if (mode_str == "basic") {
      rp.parseBasic(doc);
    }
  }
}
//Voltage detection initialization
void adc_calibration_init() {
  if (esp_adc_cal_check_efuse(ESP_ADC_CAL_VAL_EFUSE_TP) == ESP_OK) {
    printf("eFuse Two Point: Supported\n");
  } else {
    printf("eFuse Two Point: NOT supported\n");
  }
  //Check Vref is burned into eFuse
  if (esp_adc_cal_check_efuse(ESP_ADC_CAL_VAL_EFUSE_VREF) == ESP_OK) {
    printf("eFuse Vref: Supported\n");
  } else {
    printf("eFuse Vref: NOT supported\n");
  }
}

//Voltage detection
void bat_check() {
  static uint16_t bat_check_num = 2;
  if (bat_check_num > 2) {
    //Voltage reading
    uint32_t sum = 0;
    sum = analogRead(BAT_PIN);
    uint32_t voltage = esp_adc_cal_raw_to_voltage(sum, &adc_chars);
    rp.battery_voltage = (voltage * 4) / 1000.0;

    Serial.println(rp.battery_voltage);
    //Battery display
    bat_check_num = 0;
  } else
  {
    bat_check_num++;
  }
  if (rp.battery_voltage > 7.4)
  {
    digitalWrite(LED_BAT, HIGH);
  }
  else if(rp.battery_voltage > 0.5)
  {
    static uint8_t toggle;
    toggle = !toggle;
    digitalWrite(LED_BAT, toggle);
  }
  else 
  {
    digitalWrite(LED_BAT, LOW);
  }
   
}

//Generate a one-second tick
bool one_second_tick(void) {
  static unsigned long lastMillis = 0;
  unsigned long currentMillis = millis();
 
  if (currentMillis - lastMillis >= 1000) {
    lastMillis = currentMillis;
    return 1;
  }
  //Overflow handling
  if (lastMillis > currentMillis) {
    lastMillis = currentMillis;
  }

  return 0;
}
//milliseconds
bool ten_msec_tick(void) {
  static unsigned long lastMillis = 0;
  unsigned long currentMillis = millis();

  if (currentMillis - lastMillis >= 10) {
    lastMillis = currentMillis;
    return 1;
  }
  //Overflow handling
  if (lastMillis > currentMillis) {
    lastMillis = currentMillis;
  }

  return 0;
}

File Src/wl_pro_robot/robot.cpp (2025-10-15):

#include "robot.h"
#include <ArduinoJson.h>
#include "wifi.h"
#include "eeprom_util.h"
#include "Servo_STS3032.h"
#include "SPIFFS.h"
#include <vector>
#include "cpu0_task.h"
#include "ble.h"
#include "web_socket_client_util.h"
#include <MPU6050_tockn.h>

int BAT_PIN = 35;
esp_adc_cal_characteristics_t adc_chars;
Wrobot wrobot;
RobotProtocol rp(20);

RobotProtocol::RobotProtocol(uint8_t len) {
  _len = len;
  _now_buf = new uint8_t[_len];
  _old_buf = new uint8_t[_len];

  for (int i = 0; i < _len; i++) {
    _now_buf[i] = 0;
  }

  _now_buf[0] = 0xAA;
  _now_buf[1] = 0x55;
}

RobotProtocol::~RobotProtocol() {
  delete[] _now_buf;
  delete[] _old_buf;
}

void RobotProtocol::spinOnce(void) {
  int flag = checkBufRefresh();
  if (flag) {
    //UART_WriteBuf(); //This will convert the control information on the web end into a serial port protocol for transmission

    //Serial.println(wrobot.dir);//Test data acquisition
    //Serial.println("date have send\n");
    //Serial.printf("height:%d\n", wrobot.height);
    //Serial.printf("roll:%d\n", wrobot.pitch);
    //Serial.printf("linear:%d\n", wrobot.linear);
    //        Serial.printf("\n");
    //        Serial.printf("joy_X:%d\n", wrobot.joyx);
    //        Serial.printf("joy_Y:%d\n", wrobot.joyy);
  }
}









/**************The following is simultaneously used for serial port output control protocols***************/

void RobotProtocol::UART_WriteBuf(void) {
  for (int i = 0; i < _len; i++) {
    Serial.write(_now_buf[i]);
  }
}

int RobotProtocol::checkBufRefresh(void) {
  int ret = 0;
  for (int i = 0; i < _len; i++) {
    if (_now_buf[i] != _old_buf[i]) {
      ret = 1;
      break;
    } else {
      ret = 0;
    }
  }

  for (int i = 0; i < _len; i++) {
    _old_buf[i] = _now_buf[i];
  }
  return ret;
}
// This undocumented internal function must be declared
extern "C" {
  uint8_t temprature_sens_read();
}

double RobotProtocol::get_pcb_version() {
  int sensorValue = analogRead(A0);
  pcb_version = sensorValue * (3.30 / 4096) + 1;
  Serial.print("pcb_version:");
  Serial.println(pcb_version);
  return pcb_version;
}

double RobotProtocol::get_fahrenheit() {
  return temprature_sens_read();
}

double RobotProtocol::get_degree_centigrade() {
  double fahrenheit = get_fahrenheit();
  // Convert to Celsius (unit: Fahrenheit)
  return (fahrenheit - 32) / 1.8;
}

double RobotProtocol::get_battery_voltage() {
  return battery_voltage;
}

double RobotProtocol::get_battery_level() {
  double currentVoltage = battery_voltage;
  double maxVoltage = 8.3;
  double minVoltage = 7.0;

  // Ensure the voltage is within a reasonable range

  if (currentVoltage >= maxVoltage) return 100.0;
  if (currentVoltage <= minVoltage) return 0.0;

  // Calculate the percentage
  double battery_percentage = (currentVoltage - minVoltage) / (maxVoltage - minVoltage) * 100.0;

  battery_percentage = round(battery_percentage) / 1;  // Format to retain two significant digits (rounded to 2 decimal places)

  // Battery logic correction (prevent out-of-bounds and display of 0 data)
  if (battery_percentage > 100) {
    battery_percentage = 100;
  } else if (battery_percentage < 1) {
    battery_percentage = 1;
  }
  battery_level = battery_percentage;
  return battery_percentage;
}

int RobotProtocol::get_robot_status() {
  // 0 - Normal state, 1 - Primary out-of-control state (tilting), 2 - Recovery waiting state
  int robot_status = -1;
  if (uncontrolable == 0) {
    robot_status = 0;
  } else if (uncontrolable == 1) {
    robot_status = 1;
  } else if (uncontrolable > 1) {
    robot_status = 2;
  }
  return robot_status;
}


void RobotProtocol::printDoc(StaticJsonDocument<300> &doc) {
  char receive_command[300];
  serializeJson(doc, receive_command);
  Serial.printf("receive_command:%s \r\n", receive_command);
}

bool create_and_write_file(const char *filePath, const char *content) {
  // Open the file in write mode (if the file does not exist, it will be created)
  File file = SPIFFS.open(filePath, FILE_WRITE);
  // Write the content to the file
  size_t bytesWritten = file.print(content);
  file.close();
  if (bytesWritten > 0) {
    Serial.printf("Successfully wrote %d bytes to the file\n", bytesWritten);
    return true;
  } else {
    Serial.println("An error occurred while writing to the file.");
    return false;
  }
}
void RobotProtocol::save_config_json(void) {

  char json_arr[CONFIG_JSON_SIZE + 1] = { 0 };
  serializeJson(rp.config_json, json_arr);

  //seve data
  eeprom_util.write(&EepromParam.ADDR_JSON, json_arr);

  //read data
  Serial.print("read config json :");Serial.println(eeprom_util.read(&EepromParam.ADDR_JSON));
}
void RobotProtocol::save_wifi_info_json(void) {
  
  char json_arr[WIFI_INFO_JSON_SIZE + 1] = { 0 };
  serializeJson(rp.wifi_info_json, json_arr);

  //seve data
  eeprom_util.write(&EepromParam.ADDR_WIFI_INFO_JSON, json_arr);

  //read data
  Serial.print("read wifi info json :");Serial.println(eeprom_util.read(&EepromParam.ADDR_WIFI_INFO_JSON));

}
void RobotProtocol::json_is_sys_wifi(StaticJsonDocument<300> &doc) {

  wifi_info_json[WIFI_INFO_KEY.STATE]     = doc[WIFI_INFO_KEY.STATE];
  if (doc[WIFI_INFO_KEY.STATE] == WIFI_STATE.CLIENT)
  {
    wifi_info_json[WIFI_INFO_KEY.SSID]      = doc[WIFI_INFO_KEY.SSID];
    wifi_info_json[WIFI_INFO_KEY.PASSWORD]  = doc[WIFI_INFO_KEY.PASSWORD];
  }

  // save data
  String jsonStr;
  serializeJson(wifi_info_json, jsonStr);
  eeprom_util.write(&EepromParam.ADDR_WIFI_INFO_JSON, jsonStr);

  // read data
  Serial.print("READ SAVE WEB SOCKET HOST:");
  Serial.println(eeprom_util.read(&EepromParam.ADDR_WIFI_INFO_JSON));
  wifi_restart();

}
void RobotProtocol::json_is_sys_web_socket_server(StaticJsonDocument<300> &doc) {
  String host = doc["host"];
  uint16_t port = doc["port"];
  String path = doc["path"];

  // save data
  eeprom_util.write(&EepromParam.ADDR_WEB_SOCKET_HOST, host);
  eeprom_util.writeUint16T(&EepromParam.ADDR_WEB_SOCKET_PORT, port);
  eeprom_util.write(&EepromParam.ADDR_WEB_SOCKET_PATH, path);

  // read data
  Serial.print("READ SAVE WEB SOCKET HOST:");
  Serial.println(eeprom_util.read(&EepromParam.ADDR_WEB_SOCKET_HOST));
  Serial.print("READ SAVE WEB SOCKET PORT:");
  Serial.println(eeprom_util.readToUint16T(&EepromParam.ADDR_WEB_SOCKET_PORT));
  Serial.print("READ SAVE WEB SOCKET PATH:");
  Serial.println(eeprom_util.read(&EepromParam.ADDR_WEB_SOCKET_PATH));
}
void RobotProtocol::json_is_sys_set_name(StaticJsonDocument<300> &doc) {
  if (doc["name"].isNull() == true) {
    Serial.println("Invalid json data.");
  } else {
    String name_str = doc["name"];
    if (name_str.length() > 20) {
      Serial.println("The name is too long. Please limit it to 20 characters or less.");
      return;
    }
    config_json[CONFIG_KEY.NAME] = doc["name"];
    save_config_json();
  }
}

// Interrupt function - This function will be called when the time is up.
void ARDUINO_ISR_ATTR show_expression_time_callback()
{
  rp.show_expression_time = -1;
}
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

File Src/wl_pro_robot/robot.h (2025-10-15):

#pragma once

#include <WiFi.h>
#include <ArduinoJson.h>
#include "esp_adc_cal.h"
#include "feedback_util.h"
#include "eeprom_util.h"


#define CONFIG_JSON_SIZE 300
#define WIFI_INFO_JSON_SIZE 110

typedef struct {
  int height = 38;
  int roll;
  int linear;
  int angular;
  int dir;
  int dir_last;
  int joyy;
  int joyy_last;
  int joyx;
  int joyx_last;
  bool go;
  int uncontrolable = 0;  //Too much tilt and loss of control
} MemotyTabTypeDef;


typedef struct {
  int height = 38;
  int roll;
  int linear;
  int angular;
  int dir;
  int dir_last;
  int joyy;
  int joyy_last;
  int joyx;
  int joyx_last;
  bool go;
  int uncontrolable = 0;  //Too much tilt and loss of control
} Wrobot;


// Enumeration of robot motion states
typedef enum {
  FORWARD = 0,
  BACK,
  RIGHT,
  LEFT,
  STOP,
  JUMP,
} QR_State_t;


struct {

  const String SYS_WIFI = "sys_wifi";
  const String SYS_WEB_SOCKET_SERVER = "sys_web_socket_server";
  const String SYS_RESTART = "sys_restart";
  const String GET_DEVICE_INFO = "get_device_info";
  const String OFF_SERVO = "off_servo";
  const String ON_SERVO = "on_servo";
  const String CALIBRATION_SERVO = "calibrate_servo";
  const String SET_SERVO_ID1 = "set_servo_ID1";
  const String SET_SERVO_ID2 = "set_servo_ID2";

  const String SET_NAME = "set_name";
  const String SHOW_EXPRESSION = "show_expression";
  const String GET_EXPRESSION = "get_expression";
  const String SET_CLOUD_TOKEN = "set_cloud_token";
  const String SET_OPENAI_TOKEN = "set_openai_token";

  const String SET_TEST_NUMBER = "set_test_number";

} MESSAGE_TYPE;

struct {

  const String NAME = "name";
  const String WIFI_SSID = "wifi_ssid";
  const String WIFI_PASSWORD = "wifi_password";
  const String WIFI_STATE = "wifi_state";
  const String CLOUD_TOKEN = "cloude_token";
  const String OPENAI_TOKEN = "openai_token";
} CONFIG_KEY;

struct {

  const String SSID = "ssid";
  const String PASSWORD = "password";
  const String STATE = "state";
} WIFI_INFO_KEY;


// Robot mode enumeration type
typedef enum {
  BASIC = 0,
} Robot_Mode_t;

#define WIFI_CLOSE 0
#define WIFI_SERVOR 1
#define WIFI_CLIENT 2

class RobotProtocol {
public:
  double battery_voltage = 8.4f;
  double pcb_version;
  double fahrenheit;
  double centigrade;
  double battery_level;
  int status;
  int16_t offset_roll = 0;
  int uncontrolable = 0;   //Too much tilt and loss of control
  float uncontrolable_angle = 40.0f;

  bool charge = false;
  bool socket_connected = false;
  bool ble_connected = false;
  bool wifi_connected = false;
  char wifi_state      = WIFI_CLOSE;

  bool send_status_flag = false;

  String show_expression;
  int show_expression_time = -1;  //

  uint8_t test_number=0;

  StaticJsonDocument<WIFI_INFO_JSON_SIZE> wifi_info_json;
  StaticJsonDocument<CONFIG_JSON_SIZE> config_json;
  StaticJsonDocument<512> status_json;

  RobotProtocol(uint8_t len);
  ~RobotProtocol();

  void spinOnce(void);
  double get_pcb_version();
  double get_fahrenheit(void);
  double get_degree_centigrade(void);
  double get_battery_voltage(void);
  double get_battery_level(void);
  int get_robot_status(void);
  int get_expression_name(StaticJsonDocument<300> &doc);
  void get_dev_name(char dev_name[]);
  void build_dev_name(char dev_name[]);
  void config_json_init(void);
  void printDoc(StaticJsonDocument<300> &doc);
  void isSys(StaticJsonDocument<300> &doc);
  void parseBasic(StaticJsonDocument<300> &doc);
  void parseJson(StaticJsonDocument<300> &doc);
  void send_status(void);
  void send_heartbeat(void);
  void save_wifi_info_json(void);
  void json_test(char *json_arr);
  void set_test_number(StaticJsonDocument<300> &doc);
  void test_log_output(void);
private:
  uint8_t *_now_buf;
  uint8_t *_old_buf;
  uint8_t _len;
  void UART_WriteBuf(void);
  int checkBufRefresh(void);
  void save_config_json(void);
  void json_is_sys_wifi(StaticJsonDocument<300> &doc);
  void json_is_sys_web_socket_server(StaticJsonDocument<300> &doc);
  void json_is_sys_set_name(StaticJsonDocument<300> &doc);
  void json_is_sys_show_expression(StaticJsonDocument<300> &doc);
  void json_is_sys_send_expression(int send_channel);
  void json_is_sys_set_cloud_token(StaticJsonDocument<300> &doc);
  void json_is_sys_set_openai_token(StaticJsonDocument<300> &doc);
  void calibrate_servo(void);
};

extern int BAT_PIN;        // select the input pin for the ADC
extern esp_adc_cal_characteristics_t adc_chars;

extern Wrobot wrobot;
extern RobotProtocol rp;

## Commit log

2025-04-16 init
    init
    [BOM.xlsx, BOM_PCB_Controller.csv, BOM_PCB_Encoder.csv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]
2025-09-13 Optimization and addition of functions
    Calibrate roll and yaw control, reset, add function for modifying servo ID
    [cpu0_task.cpp, robot.cpp, wl_pro_robot.ino]
2025-10-09 disable auto standup
    Set the uncontrolled angle threshold to ±25°, and beyond this angle, it will no longer attempt to balance, thus cutting off power output and restarting after assisted balancing
    [wl_pro_robot.ino]
2025-10-15 Adjust the uncontrolable angle to variable, add debug log, screen warning low battery
    [MotorBase-Aluminum6061.stp]
2026-06-07 Update BOM with Alibaba.com sources
    - Switched 22 BOM line items from Amazon/Taobao to Alibaba.com sources
    - Added a Notes column with sourcing rationale per item
    - Preserved Part Name / Specifications / Quantity from the original BOM
    - Generated by tools/update_bom.py (kept in repo for reproducibility)
    [BOM.xlsx]
2026-06-08 Update BOM
    [BOM.xlsx]
2026-06-11 Modify the model file
    [#Large_Wheel.stl, #Large_Wheel_CalfL.stl, #Large_Wheel_CalfR.stl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]
